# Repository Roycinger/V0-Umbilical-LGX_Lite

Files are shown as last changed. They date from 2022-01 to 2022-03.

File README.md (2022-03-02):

# V0-Umbilical-LGX_Lite
 
### Toolhead PCB BOM
| Part | Quantity | Notes | Digikey Part Number | Link |
| --- | :-: | --- | --- |--- |
| 16 Pin Socket (Right Angle) | 1 |  Molex 1053141316  | WM15165-ND | https://www.digikey.com/en/products/detail/molex/1053141216/6164254?s=N4IgTCBcDaIIwAYCsBmOAWOY4DYQF0BfIA |
| 2 pin JST XH | 6 |  B2B-XH  | 455-2273-ND | https://www.digikey.com/en/products/detail/jst-sales-america-inc/B2B-XH-AM-LF-SN/1016630 |
| 3 pin JST XH | 1 |  B3B-XH  | 455-2248-ND | https://www.digikey.com/en/products/detail/jst-sales-america-inc/B3B-XH-A-LF-SN/1651046 |
| 4 pin JST XH | 1 |  B4B-XH  | 455-2249-ND | https://www.digikey.com/en/products/detail/jst-sales-america-inc/B4B-XH-A-LF-SN/1651047 |

### Frame PCB BOM
| Part | Quantity | Notes | Digikey Part Number | Link |
| --- | :-: | --- | --- |--- |
| 16 Pin Socket |  1 | MOLEX 1053101216 | WM15060-ND | https://www.digikey.com/en/products/detail/molex/1053101216/6164149?s=N4IgTCBcDaIIwAYCsBmRcxwGwgLoF8g |
| SMD Thermistor  |  1 | 100K 0805 Thermistor | BC2562CT-ND | https://www.digikey.com/en/products/detail/vishay-beyschlag-draloric-bc-components/NTCS0805E3104FXT/2237371 |
| 2 pin JST XH |  5 | 2.5mm pitch | 455-2273-ND | https://www.digikey.com/en/products/detail/jst-sales-america-inc/B2B-XH-AM-LF-SN/1016630 |
| 3 pin JST XH |  3 | 2.5mm pitch | 455-2248-ND | https://www.digikey.com/en/products/detail/jst-sales-america-inc/B3B-XH-A-LF-SN/1651046 |
| 4 pin JST XH |  3 | 2.5mm pitch | 455-2249-ND | https://www.digikey.com/en/products/detail/jst-sales-america-inc/B4B-XH-A-LF-SN/1651047 |
| Screw Terminal  |  1 | 5.08mm pitch | 277-1247-ND | https://www.digikey.com/en/products/detail/phoenix-contact/1729128/260615 |

### Optional Parts
| Part | Quantity | Notes | Digikey Part Number | Link |
| --- | :-: | --- | --- |--- |
| 0805 10uF Capacitor  |  3 | Not required for Neopixel Strips | 1276-2399-1-ND | https://www.digikey.com/en/products/detail/samsung-electro-mechanics/CL21A106KOCLRNC/3888057 |

### Cable BOM
| Part | Quantity | Notes | Digikey Part Number | Link |
| --- | :-: | --- | --- |--- |
| 16 pin Plug  |  2 | Molex 1053081216 | WM15025-ND | https://www.digikey.de/de/products/detail/molex/1053081216/6164114?s=N4IgTCBcDaIIwAYCsBmBAOOY4DYQF0BfIA |
| Nanofit Crimp  |  32 | Molex 1053002200 | WM14957CT-ND | https://www.digikey.de/de/products/detail/molex/1053002200/6131599 |
| 20AWG Wire  |  16 | 200-220mm sections. Smaller wire (i.e.24AWG can be used. Make sure to user proper wire size for heater and ground wires | |  |

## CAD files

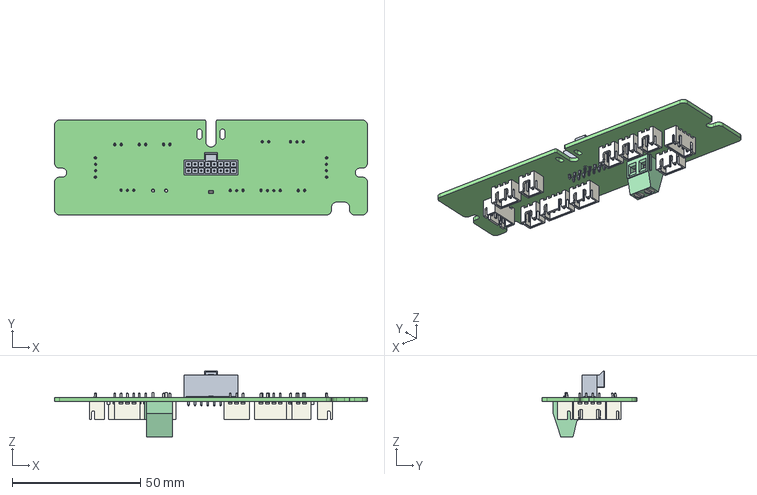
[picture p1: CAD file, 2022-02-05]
Frame_PCB/V0-UmbilicalBoard.step
122.0 x 37.0 x 25.7 mm

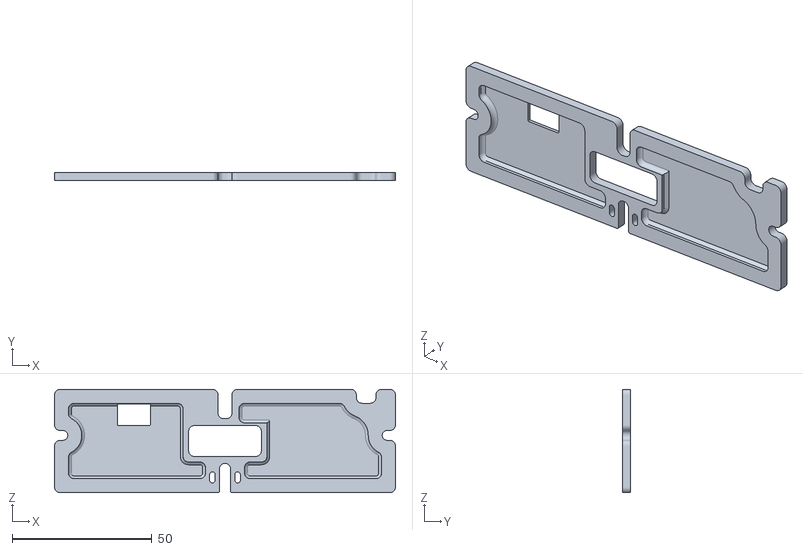
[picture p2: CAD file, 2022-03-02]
STLs/FramePCBCover_topHole.stl
122.0 x 3.00 x 37.0

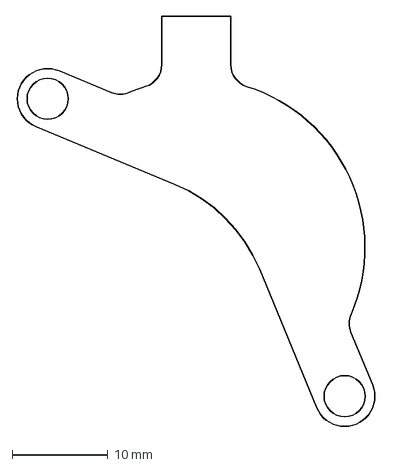
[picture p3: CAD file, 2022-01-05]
strain_relief.dxf
37.6 x 42.9 mm

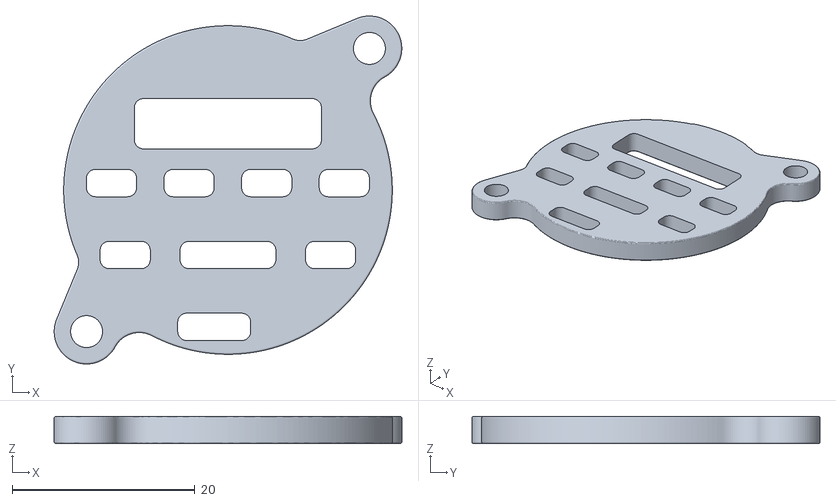
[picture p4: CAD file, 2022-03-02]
STLs/ToolheadSpacer.stl
38.1 x 38.1 x 3.00

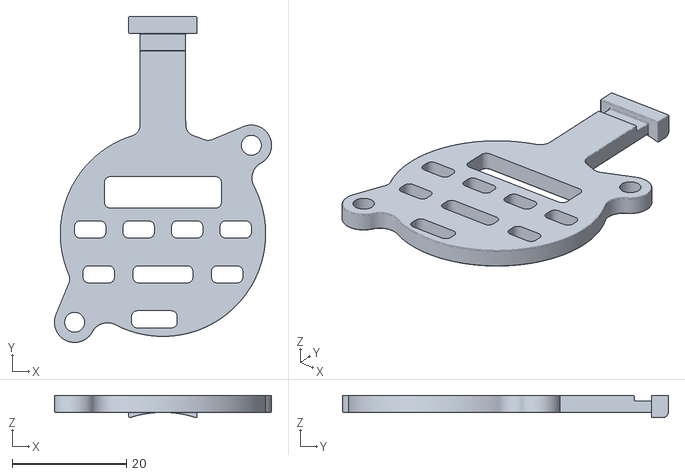
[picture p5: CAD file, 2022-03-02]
STLs/ToolheadSpacer_StrainRelief.stl
38.1 x 57.1 x 3.92

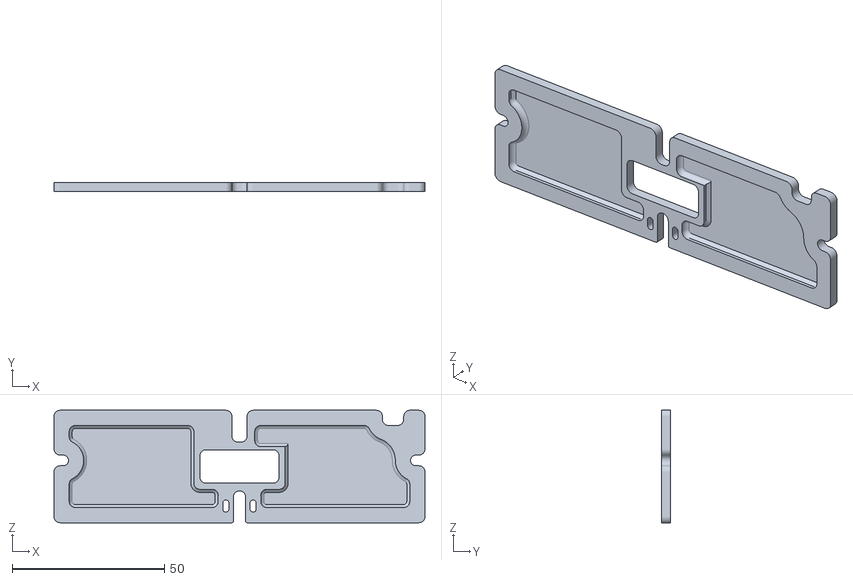
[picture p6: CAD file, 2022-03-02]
STLs/FramePCBCover.stl
122.0 x 3.00 x 37.0

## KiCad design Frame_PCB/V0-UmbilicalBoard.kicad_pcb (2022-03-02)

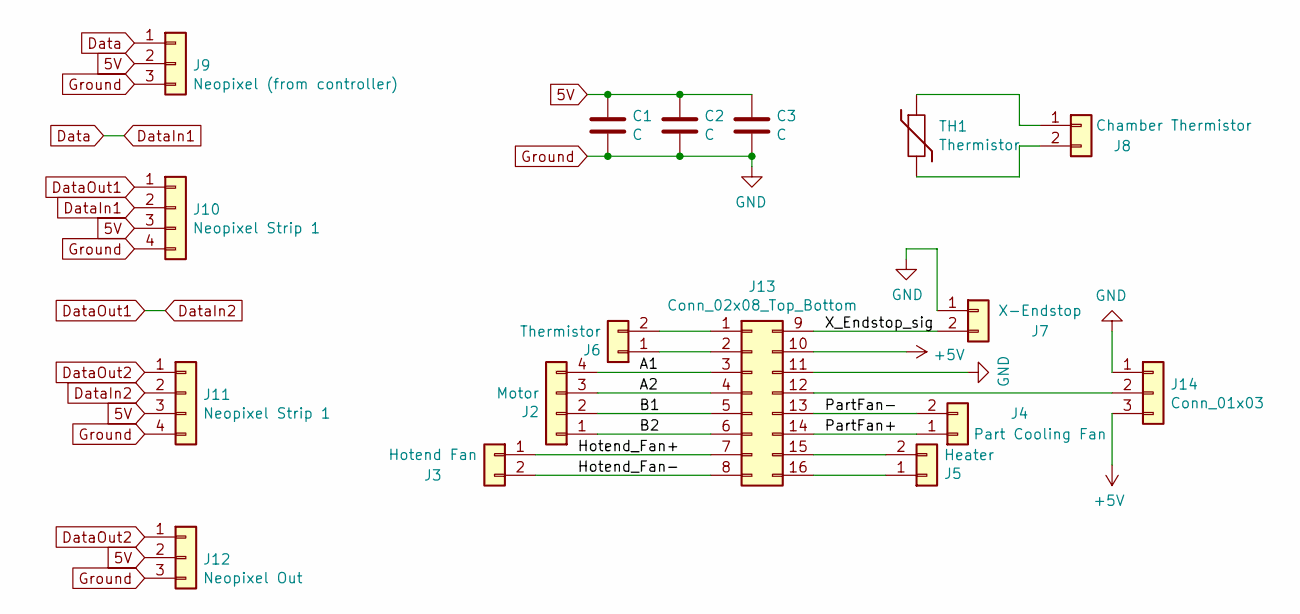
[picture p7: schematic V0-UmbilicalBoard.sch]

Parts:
C1, C2, C3: C; C_0805_2012Metric_Pad1.18x1.45mm_HandSolder
J2: Motor; JST_XH_B4B-XH-A_1x04_P2.50mm_Vertical
J3: Hotend Fan; JST_XH_B2B-XH-A_1x02_P2.50mm_Vertical
J4: Part Cooling Fan; JST_XH_B2B-XH-A_1x02_P2.50mm_Vertical
J5: Heater; TerminalBlock_Phoenix_MKDS-1,5-2-5.08_1x02_P5.08mm_Horizont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
J6: Thermistor; JST_XH_B2B-XH-A_1x02_P2.50mm_Vertical
J7: X-Endstop; JST_XH_B2B-XH-A_1x02_P2.50mm_Vertical
J8: Chamber Thermistor; JST_XH_B2B-XH-A_1x02_P2.50mm_Vertical
J9: Neopixel (from controller); JST_XH_B3B-XH-A_1x03_P2.50mm_Vertical
J10, J11: Neopixel Strip 1; JST_XH_B4B-XH-A_1x04_P2.50mm_Vertical
J12: Neopixel Out; JST_XH_B3B-XH-A_1x03_P2.50mm_Vertical
J13: Conn_02x08_Top_Bottom; Molex_Nano-Fit_105310-xx16_2x08_P2.50mm_Vertical
J14: Conn_01x03; JST_XH_B3B-XH-A_1x03_P2.50mm_Vertical
TH1: Thermistor; R_0805_2012Metric_Pad1.20x1.40mm_HandSolder

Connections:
5V: C1.1, C2.1, C3.1, J9.2, J10.3, J11.3, J12.2
+5V: J13.10, J14.3; also elsewhere on the board
/A1: J2.4, J13.3
/A2: J2.3, J13.4
/B1: J2.2, J13.5
/B2: J2.1, J13.6
/Hotend_Fan+: J3.1, J13.7
/Hotend_Fan-: J3.2, J13.8
/KlickySignal: J13.12, J14.2; also elsewhere on the board
/PartFan+: J4.1, J13.14
/PartFan-: J4.2, J13.13
/X_Endstop_sig: J7.2, J13.9
Data: J9.1, J10.2
DataIn2: J10.1, J11.2
DataOut2: J11.1, J12.1
Ground: C1.2, C2.2, C3.2, J7.1, J9.3, J10.4, J11.4, J12.3, J13.11, J14.1; also elsewhere on the board
unnamed: J8.1, TH1.1
unnamed: J8.2, TH1.2
unnamed: J6.2, J13.1
unnamed: J6.1, J13.2
unnamed: J5.2, J13.15
unnamed: J5.1, J13.16

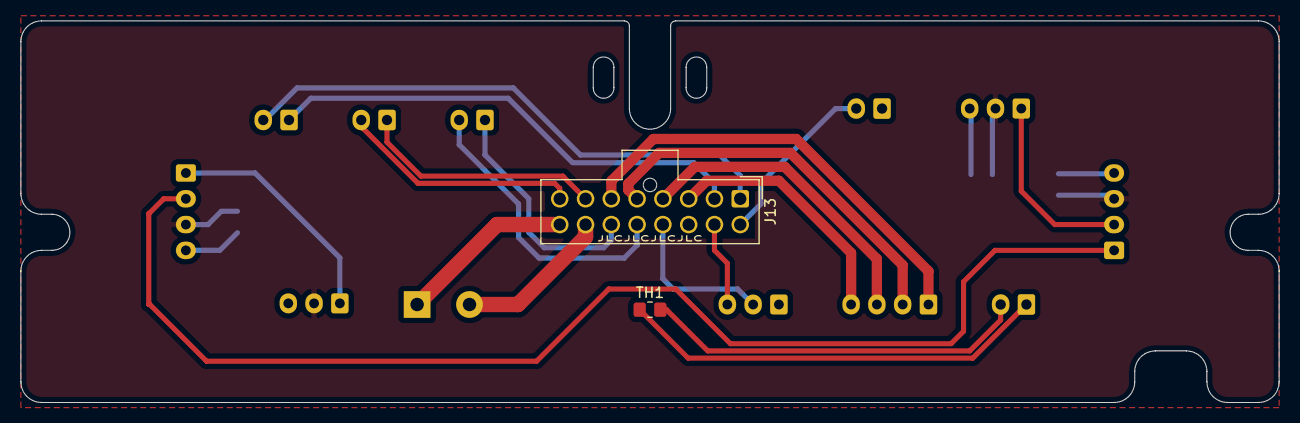
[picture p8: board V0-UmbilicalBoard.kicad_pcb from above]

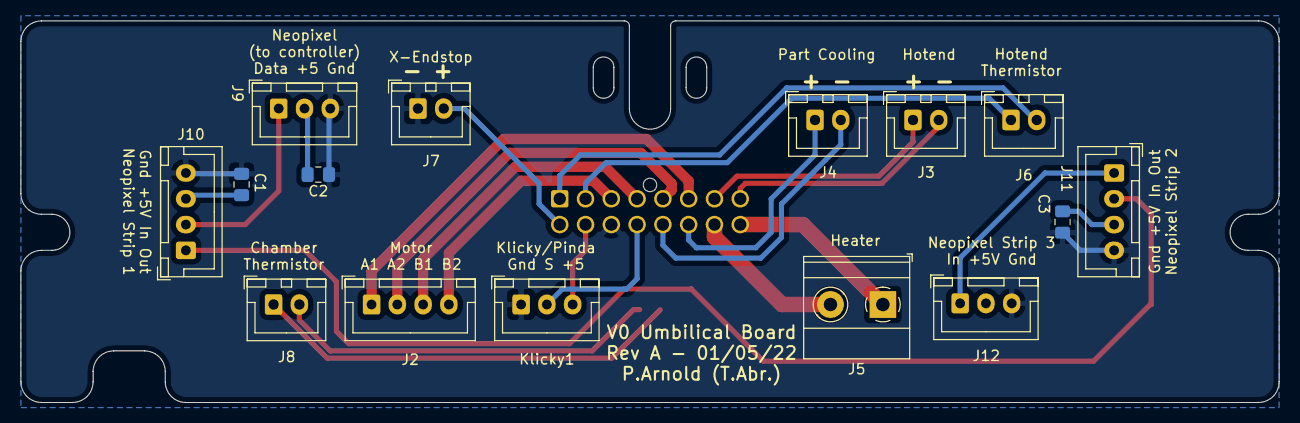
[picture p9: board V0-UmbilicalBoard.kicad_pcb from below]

Board: 2 copper layers, 122.0 x 37.0 mm, 17 parts (15 on the bottom side), 22 nets.

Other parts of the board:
Klicky1: Conn_01x03; JST_XH_B3B-XH-A_1x03_P2.50mm_Vertical

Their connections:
+5V: Klicky1.3; also elsewhere on the board
/KlickySignal: Klicky1.2; also elsewhere on the board
Ground: Klicky1.1; also elsewhere on the board

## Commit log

2022-01-05 Some adjustments
    [Toolhead_PCB_new.step, V0-UmbilicalBoard.kicad_pcb, V0-UmbilicalBoard.sch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]
2022-02-05 changed hotend fan silkscreen lettering
    + and - were swapped unintentionally
    [Toolhead_PCB-B_Cu.gbl, Toolhead_PCB-B_Mask.gbs, Toolhead_PCB-B_Paste.gbp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]
2022-02-05 minor schematic correction
    renamed wire label "Clicky_Sig" to "Klicky_Sig" on the Toolhead PCB
    [Toolhead_PCB.sch]
2022-03-02 uploaded STLs
    STLs for toolhead spacers and frame PCB cover.
    FramePCBCover_topHole.stl features a hole in the cover to solder a 3-pin JST-XH on the opposite side for routing a servo cable to the print chamber (i.e. nozzle wiper arm mechanism)
    [FramePCBCover.stl, FramePCBCover_topHole.stl, ToolheadSpacer.stl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]
